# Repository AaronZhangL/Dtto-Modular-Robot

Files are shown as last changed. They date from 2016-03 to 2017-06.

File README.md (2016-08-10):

# Dtto Modular Robot
Dtto Robot v1.0 , a modular self-reconfigurable robot

A better and up to date description is available at: 
https://hackaday.io/project/9976-dtto-v10-modular-robot

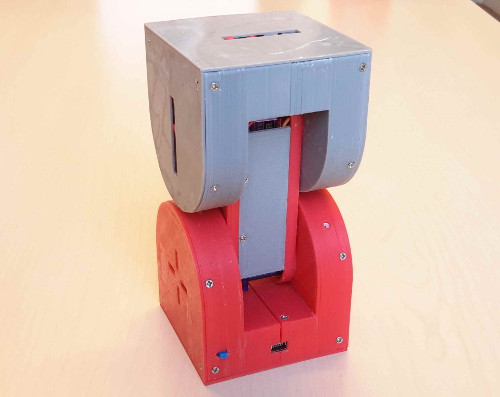
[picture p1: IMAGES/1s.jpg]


The <strong>Dtto v1.0 </strong> Robot is a modular transformable robot designed to be versatile, flexible and <strong>self-reconfigurable</strong>. The idea of modular robots is that they can adopt any shape they want, by changing the position and the connection of their modules. 

This robot is aimed for <strong>research</strong> on modular self-reconfigurable robots and educational purposes. It is designed to allow multiple modules to communicate, mechanically connect and disconnect and to work collaboratively in the locomotion, self-reconfigurability and efficient movement.

The versatility of the robot will allow it, in the future, to be able to perform <strong>rescue operations</strong>, exploration of unknown environments and <strong>space exploration</strong>.

In <strong>future</strong> works, the modules will have built in camera, ultra-sound sensor, gyroscope, accelerometer, magnetometer… The possibilities are endless.
 
This is a part of a project that is currently being developed in the <strong>Universitat Rovira i Virgili</strong>, Tarragona (Spain).

Special thanks to my project director, Dr. Jose Luís Ramírez, and to Dr. Juan González-Gómez “Obijuan”, for their support and help everytime I needed it. 

It has been fully printed with open-source 3D printers, uses open-source hardware and has been designed entirely on FreeCad.

This robot is Inspired by the MTRAN III, by The National Institute of Advanced Industrial Science and Technology (AIST), Japan. (https://unit.aist.go.jp/is/frrg/dsysd/mtran3/index.htm)

Follow the project: https://hackaday.io/project/9976-dtto-v10-modular-robot

#SPECIFICATIONS

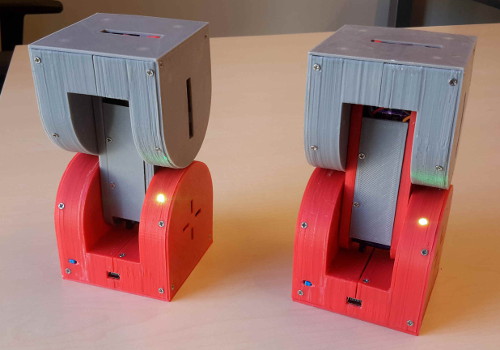
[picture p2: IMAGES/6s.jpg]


- Dimensions: 64* x 64 x 130 mm
- Weight: 210gr approx
- 2 servos TowerPro SG92R main movement (2.5kg/cm)
- 3 servos TowerPro SG90 coupling mechanism (1.8kg/cm)
- 24 Alignment magnets (4x3 neodymium disc)
- 1 Arduino nano v3.0
- 1 Bluetooth HC-06
- 1 RF. NRF2401+
- 1 WS2812 LED RGB

#VIDEOS

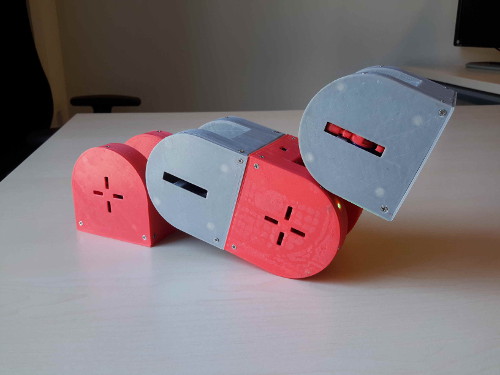
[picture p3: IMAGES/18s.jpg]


Three modules rolling
https://www.youtube.com/watch?v=pWOIe7kMd5U

One module moving, connection mechanism:
https://www.youtube.com/watch?v=O0k1wR8lxH4

Two modules connecting, moving and disconecting:
https://www.youtube.com/watch?v=2cLM48vNh7w

#CONFIGURATIONS

This is a small model showing some of the different configurations of the robot.

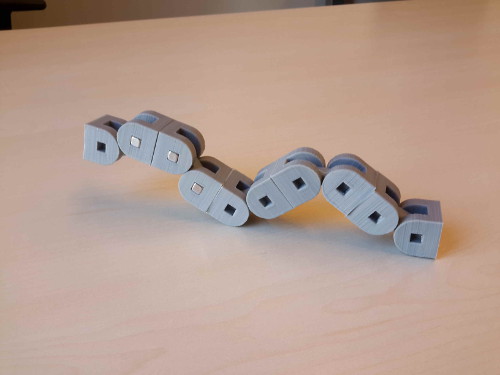
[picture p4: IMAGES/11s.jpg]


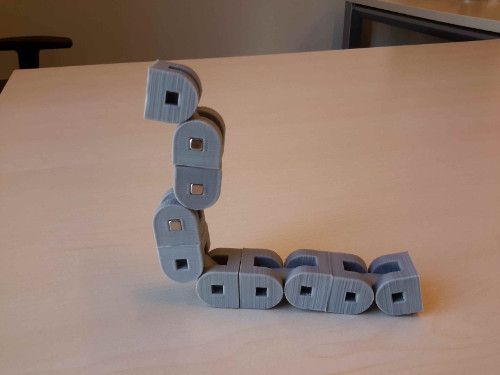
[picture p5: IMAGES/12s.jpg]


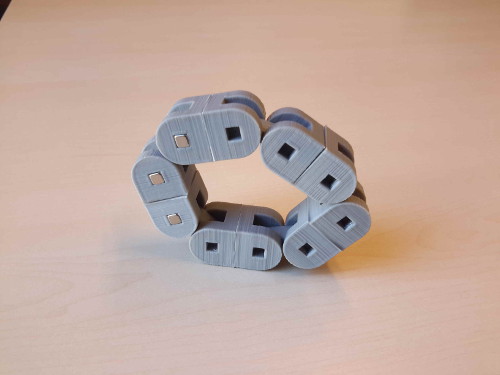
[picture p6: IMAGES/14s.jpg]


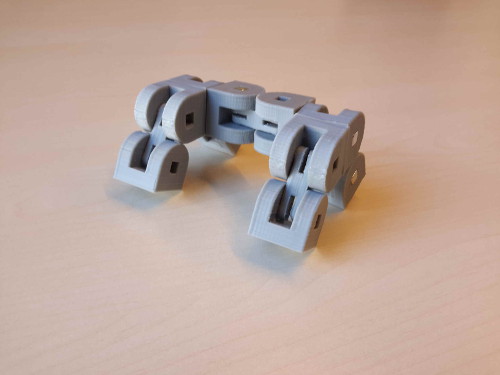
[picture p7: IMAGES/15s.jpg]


#LICENSE

This project and all of it's files, images and texts are entirely licensed under the CC BY-SA 4.0 license. (http://creativecommons.org/licenses/by-sa/4.0/legalcode)

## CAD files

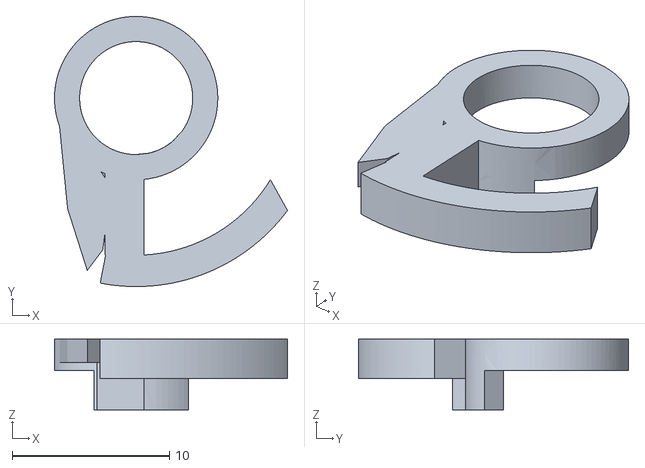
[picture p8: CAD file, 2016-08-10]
3D-printing/Dtto-v2.0.1/014-1(ganchoB001).stl
14.8 x 17.2 x 4.50

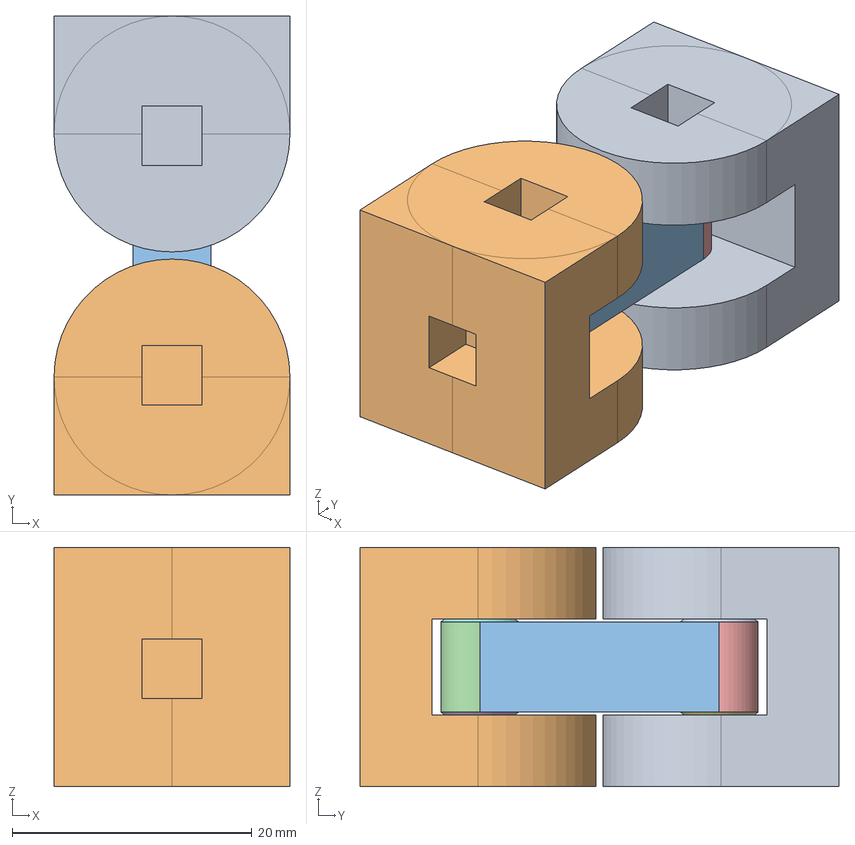
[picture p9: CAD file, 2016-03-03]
3D-printing/Freecad-files/Modelo.Escala.Dtto.v1.1.FCStd
19.7 x 40.0 x 20.0 mm
Cubo004
Cilindro002
Clone of Cilindro002
Cono001
Clone of Cono002
Clone of Cono003
Clone of Clone of Cono003

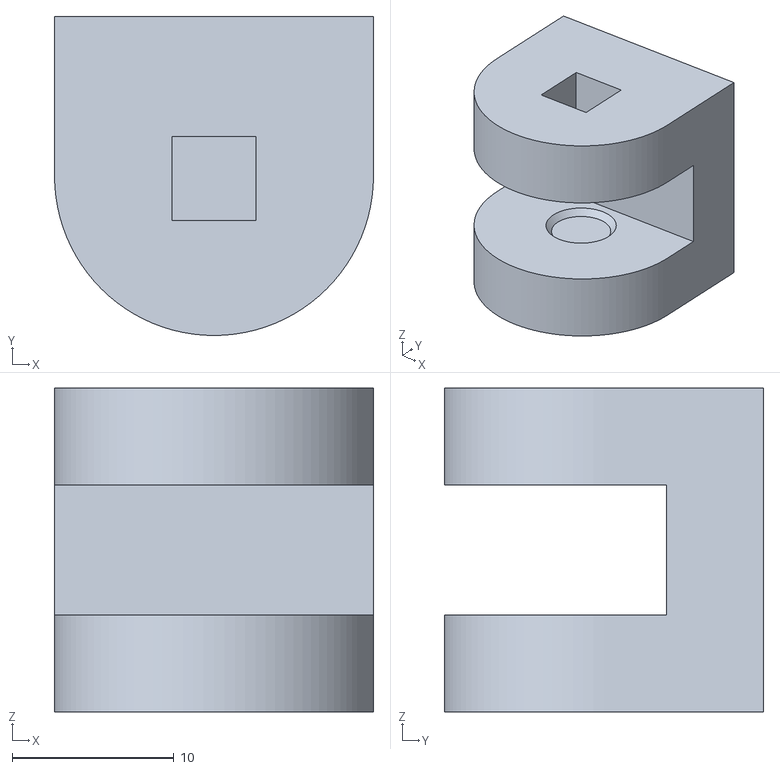
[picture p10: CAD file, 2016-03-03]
3D-printing/Small-model-v1/Male004.stl
19.7 x 19.7 x 20.0

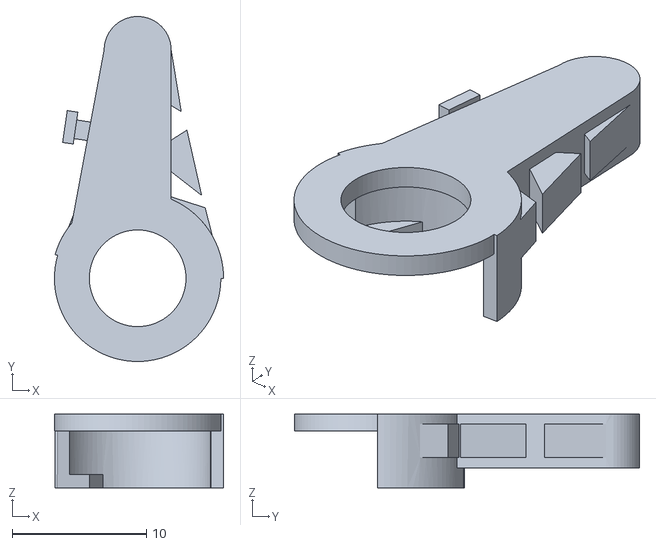
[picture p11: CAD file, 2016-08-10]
3D-printing/Dtto-v2.0.1/013-1(ganchoA002).stl
12.6 x 25.7 x 5.50

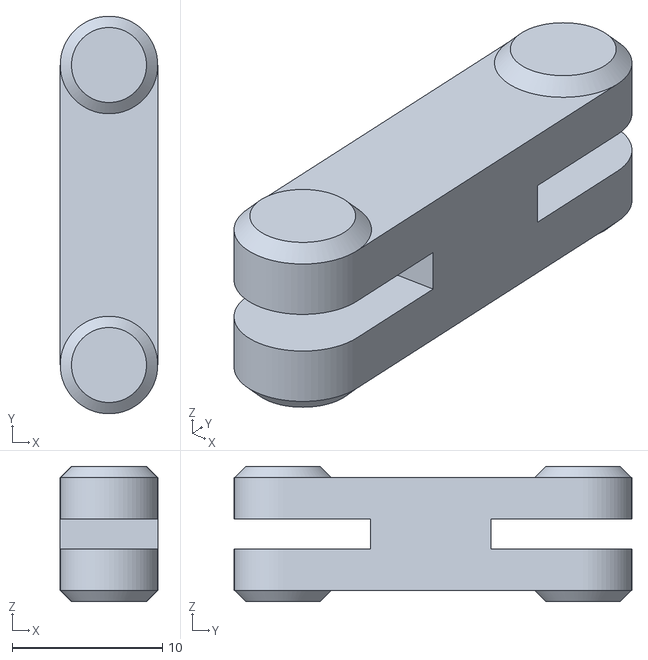
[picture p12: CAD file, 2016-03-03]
3D-printing/Small-model-v1/Brazo002.stl
6.50 x 26.5 x 9.00

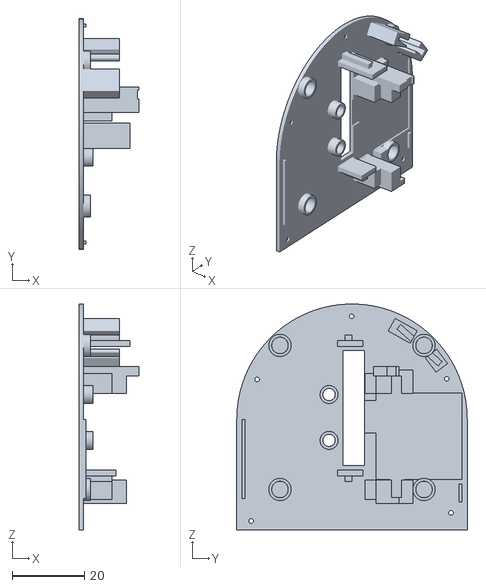
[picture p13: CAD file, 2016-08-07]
3D-printing/Dtto-v2.0.1/007-1(paredAM001).stl
16.8 x 64.0 x 62.8

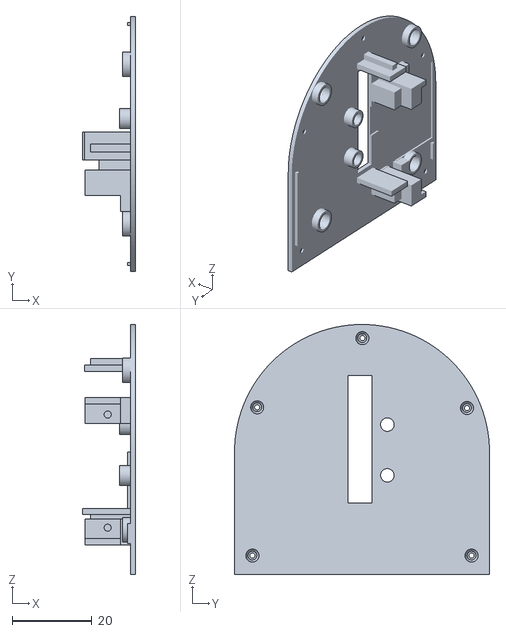
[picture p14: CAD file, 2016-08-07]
3D-printing/Dtto-v2.0.1/009-1(ParedBM001).stl
13.2 x 64.0 x 62.8

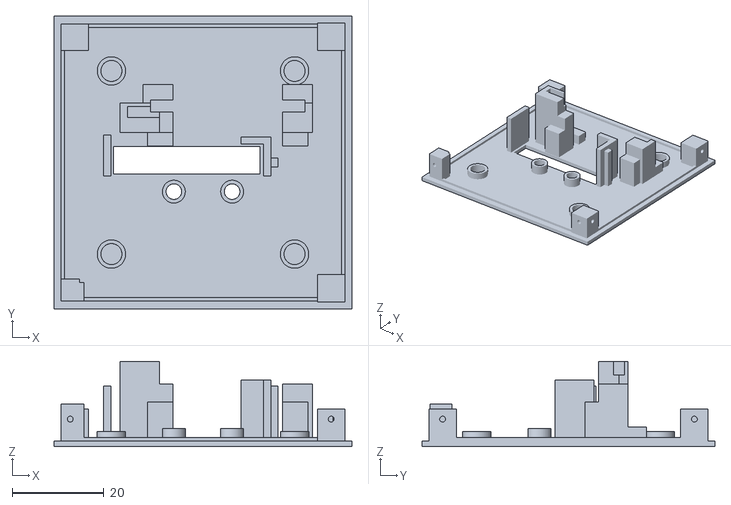
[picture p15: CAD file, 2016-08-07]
3D-printing/Dtto-v2.0.1/005-1(baseM001).stl
65.0 x 64.0 x 18.6

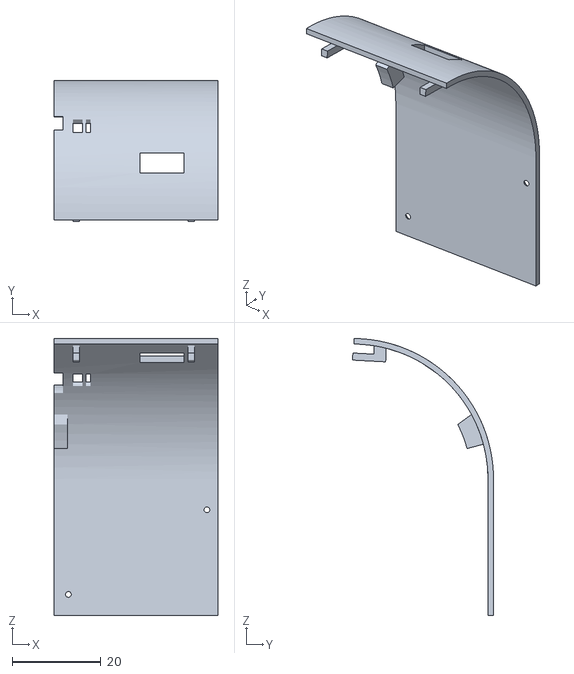
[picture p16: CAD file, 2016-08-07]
3D-printing/Dtto-v2.0.1/001-1(curvaext002).stl
37.0 x 31.8 x 62.5

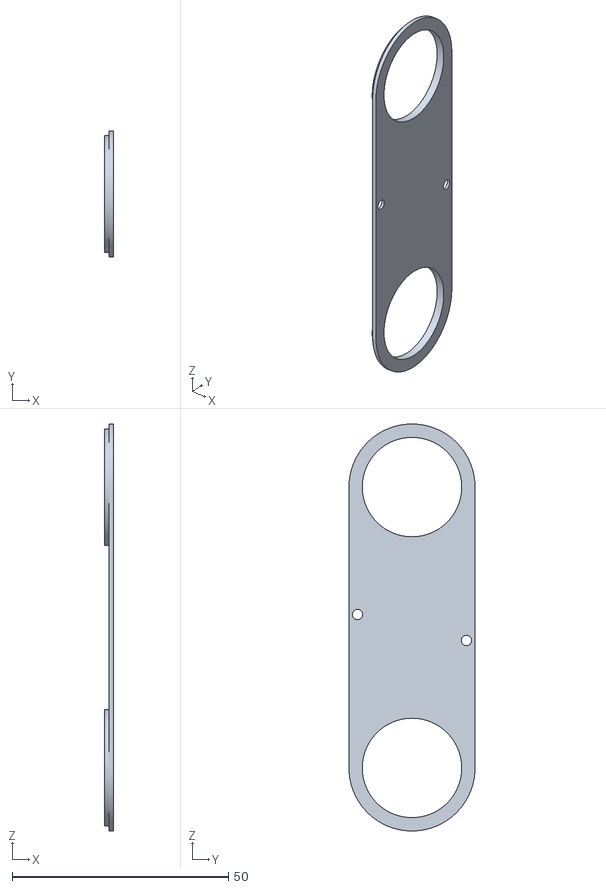
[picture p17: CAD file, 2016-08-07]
3D-printing/Dtto-v2.0.1/011-1(brazotapa002).stl
2.00 x 29.2 x 94.2

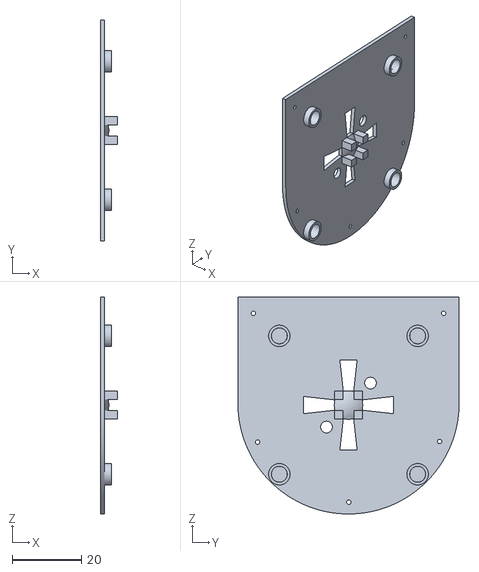
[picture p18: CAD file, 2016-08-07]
3D-printing/Dtto-v2.0.1/008-1(paredAF001).stl
5.00 x 64.0 x 62.8

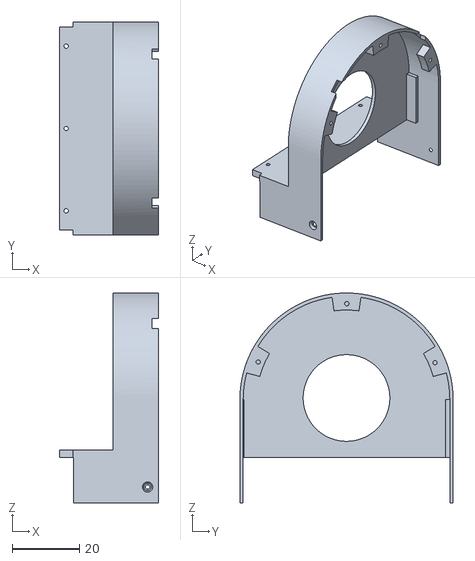
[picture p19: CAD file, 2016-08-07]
3D-printing/Dtto-v2.0.1/003-1(paredcurva003).stl
29.5 x 63.5 x 62.5

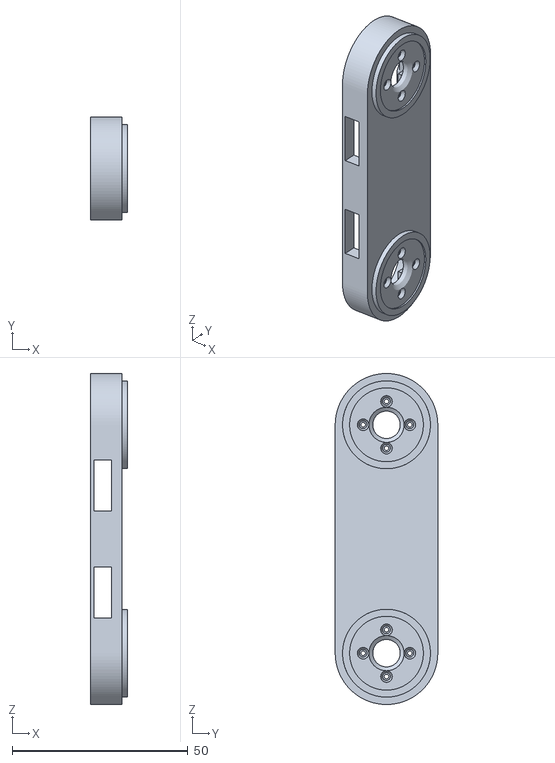
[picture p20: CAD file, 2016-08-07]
3D-printing/Dtto-v2.0.1/012-1(brazobase002).stl
10.5 x 29.2 x 94.2

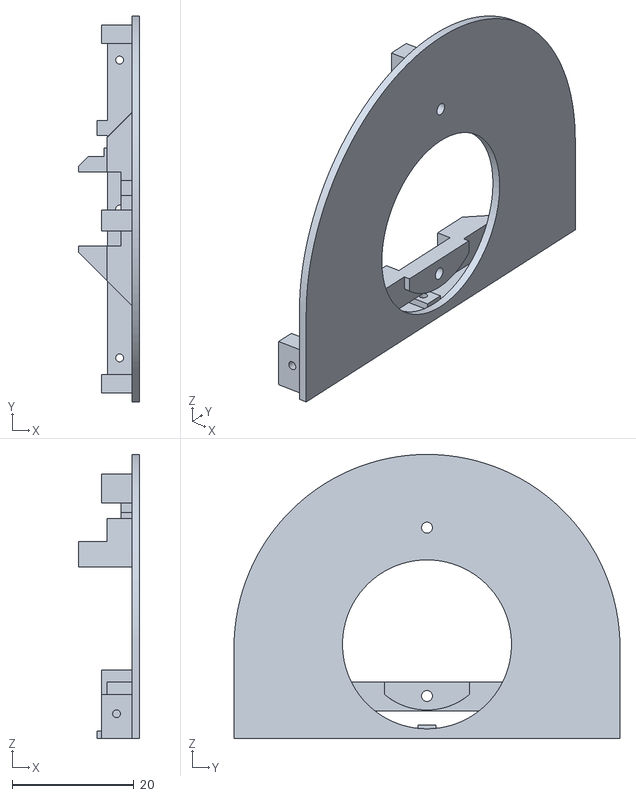
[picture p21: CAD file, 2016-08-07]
3D-printing/Dtto-v2.0.1/004-1(interior001).stl
10.0 x 63.5 x 46.8

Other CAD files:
3D-printing/Dtto-v2.0.1/002-1(curvafija002).stl
3D-printing/Dtto-v2.0.1/010-1(paredBF001).stl
3D-printing/Dtto-v2.0.1/006-1(baseF001).stl
3D-printing/Dtto-v1/ParedAM003.stl
3D-printing/Dtto-v1/CurvaAF003.stl
3D-printing/Dtto-v1/CurvaAM002.stl
3D-printing/Dtto-v1/CurvaBF003.stl
3D-printing/Dtto-v1/CurvaBM002.stl
3D-printing/Dtto-v1/ParedAF001.stl
3D-printing/Dtto-v1/ParedBF001.stl
3D-printing/Dtto-v1/ParedBM003.stl
3D-printing/Dtto-v1/baseF004.stl
3D-printing/Dtto-v1/baseM004.stl
3D-printing/Dtto-v1/brazoA001.stl
3D-printing/Dtto-v1/brazoA002.stl
3D-printing/Dtto-v1/brazoB002.stl
3D-printing/Dtto-v1/brazoBase002.stl
3D-printing/Dtto-v1/brazotapa001.stl
3D-printing/Dtto-v1/ganchoA006.stl
3D-printing/Dtto-v1/ganchoB006.stl

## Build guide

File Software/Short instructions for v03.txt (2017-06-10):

Hello!

First you should know that there is a 'master' module that you configure in the 'DttoType' definition (line 21 of 
v03 code). If you only have one module, this DttoType should be '0' (master). If you add more modules, you should 
program them with DttoType '1' (slave).

When they are connected, each module gets a number depending on the connection order (1,2,3...).

The bluetooth commands go to the rxData char array, and work like this:

- 1st character(rxData[0]): Char identifying the module you want to talk to. Ej. If you want to talk to module 1, 
this char should be '1'. If you want to talk to all the modules at the same time, you have to use athe char 'a' (all).

- 2nd character (rxData[1]):  This char is the action that the modules, or all modules, have to do. In the main 
loop 'void loop()' you have a switch case that, depending on the char on rxData[1], calls a function on the code. 
For example, if you want to call the test function, this char should be 't'.
    Command list 'rxData[1]' :
      - 's' start. moves all servomotors to the central position
      - 'r' run. starts snake movenent; 'rxData[2]' must indicate direction('m' or 'f')
      - 'e' escape. stops all other functions.
      - 'g' gancho (hook). Moves the hooks of the mechanical connection; 
        -'rxData[2]' must indicate which hook to move ('b' base, 'r' right face, 'l' left face)
        -'rxData[3]' must indicate which position to move the hook to ('0' center(hide), '1' and '2' couple or decouple)
      - 't' test. test the RGB LED on the modules
      - 'a' amplitude (experimental). change amplitude of the sinusoidal movement
      - 'f' fase (phase). change phase between motors of the sinusoidal movement

- 3rd, 4th,5... char: These characters are used as parameters in some functions, so you have to check in every 
function what does exactly do.

Examples of instructions:
  - 'arm' (All-Run-Male) starts snake movement in the male direction
  - 'at' (All-Test) blinks the RGB LED
  - '2gb0' (2ndmodule-Gancho(hook)-Base-0)moves the hook of the 2nd module to the central position
  - 'ae' (All-Escape) stops all functions, motors, LEDs of all motors.

Sorry for the bad commented code, I still have to fix it a LOT...

Alberto (10-06-2017)

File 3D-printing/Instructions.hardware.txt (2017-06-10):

*****by otrebla 333 - 03/03/2016 *****

These files have been designed to print with my personal printer,a Prusa i3
with a 0.4 nozzle and using ABS. I've printed all of them at a .25 mm layer
height.

The assembly of the parts is very simple, but the tricky part is how to manage
all the cables throught the arm. 

I will be creating the instrucions in this file as you ask.

The actual model is the 2.0.1 There will be updates soon.

There is a small model to print and simulate the big robot! 

Thanks!

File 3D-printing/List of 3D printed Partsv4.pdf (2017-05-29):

### Dtto Modular Robot - 3D Printed Parts Needed (v2.0.1)

Here there is a listing of all the 3D parts needed for building a module. They are positioned the way we think it will be best for FDM printing.

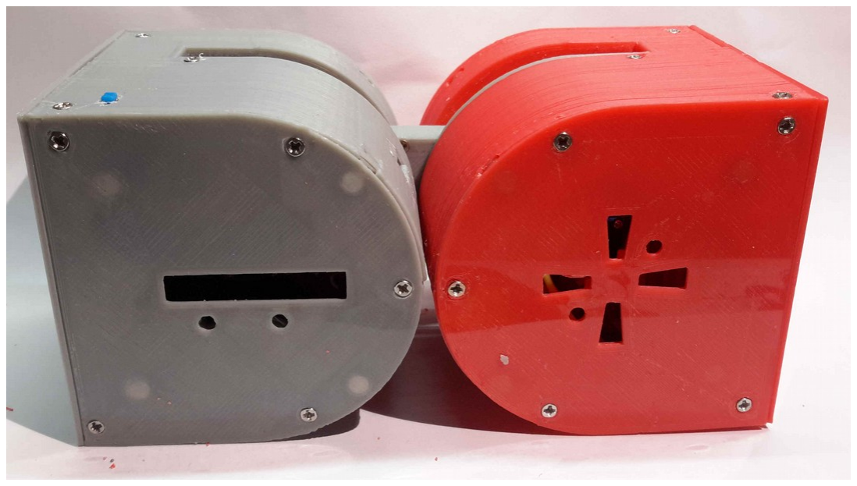
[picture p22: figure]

The module on the above picture was printed in two colours: A: Grey; B: Red.

The parts files are available for download at: https://github.com/otrebla333/Dtto-Modular-Robot Project:
https://hackaday.io/project/9976-dtto-v20-modular-robot

The parts were usually printed at 0.2mm layer height, 0.4mm nozzle size. Some parts require sanding in order to fit/slide properly.

QTY = Quantity
Part Nº | QTY | Color | Part Name | Position
001-1 | 2 | A & B | curvaext002.stl (support everywhere)

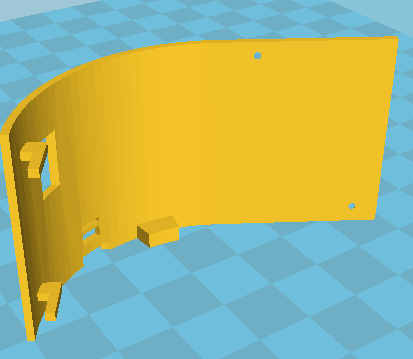
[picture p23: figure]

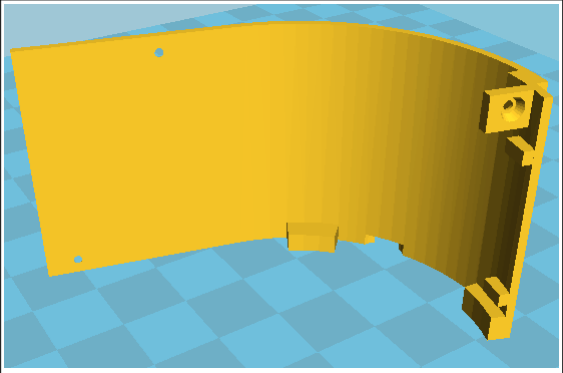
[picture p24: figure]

002-1 | 2 | A & B | curvafija002.stl (support everywhere)

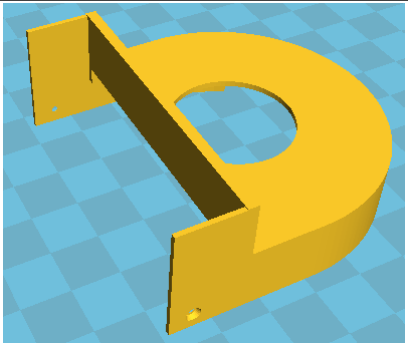
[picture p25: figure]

003-1 | 2 | A & B | paredcurva003. stl (support touching buildplate)

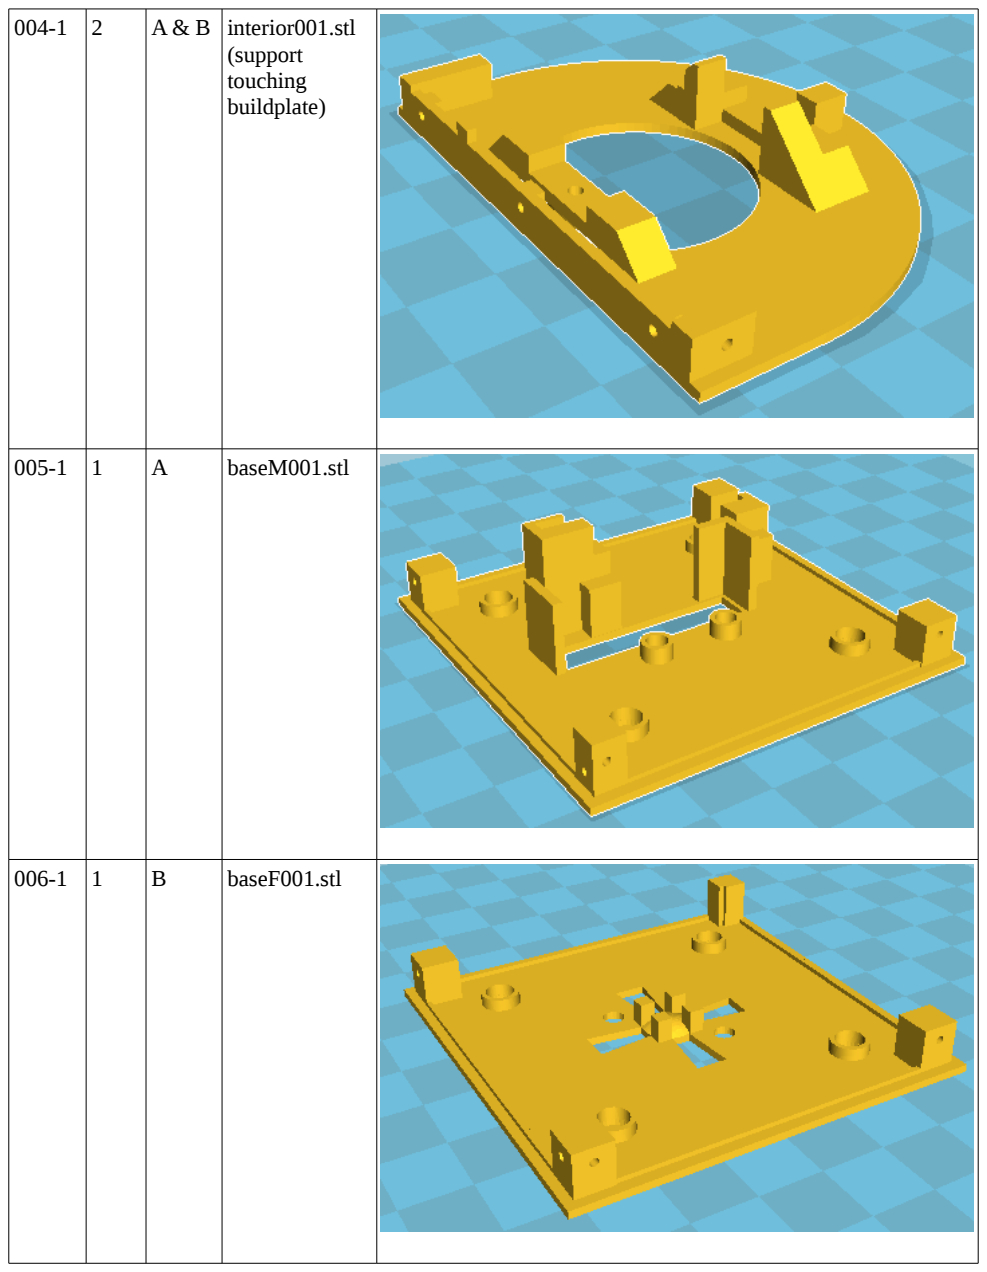
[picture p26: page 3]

004-1 | 2 | A & B | interior001.stl (support touching buildplate)
005-1 | 1 | A | baseM001.stl
006-1 | 1 | B | baseF001.stl

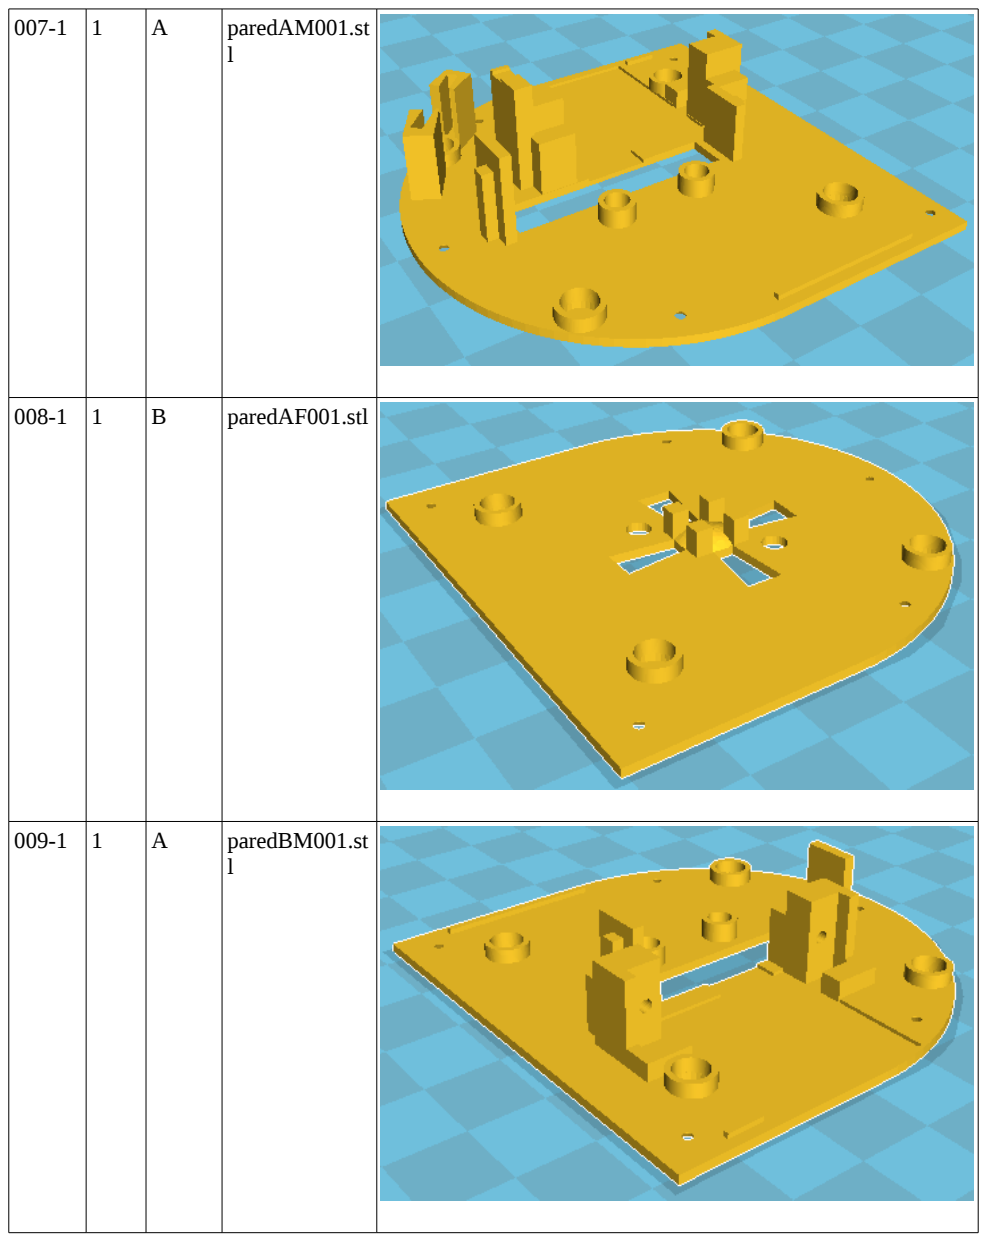
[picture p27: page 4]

007-1 | 1 | A | paredAM001.st l
008-1 | 1 | B | paredAF001.stl
009-1 | 1 | A | paredBM001.st l

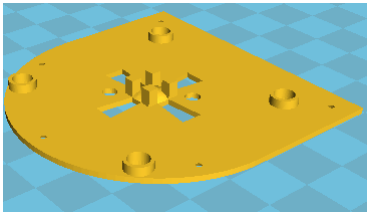
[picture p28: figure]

010-1 | 1 | B | paredBF001.stl

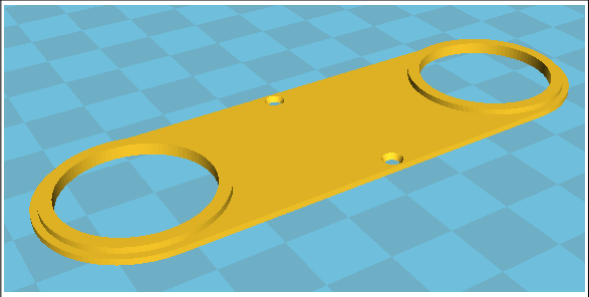
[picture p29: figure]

011-1 | 1 | A or B | brazotapa002.st l

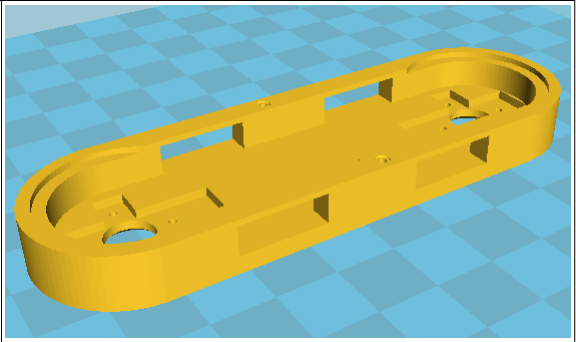
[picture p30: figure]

012-1 | 1 | A or B | brazobase002.s tl (support everywhere)

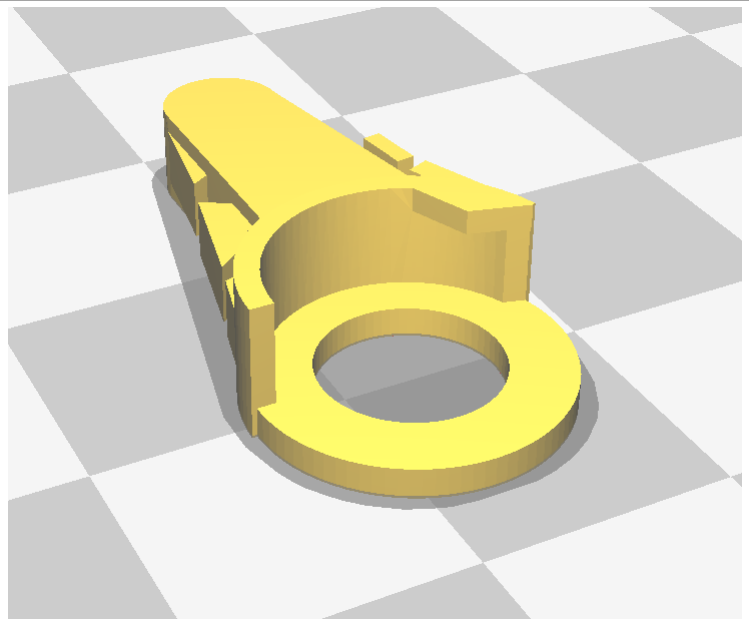
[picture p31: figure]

013-1 | 3 | A or B | ganchoA002.stl

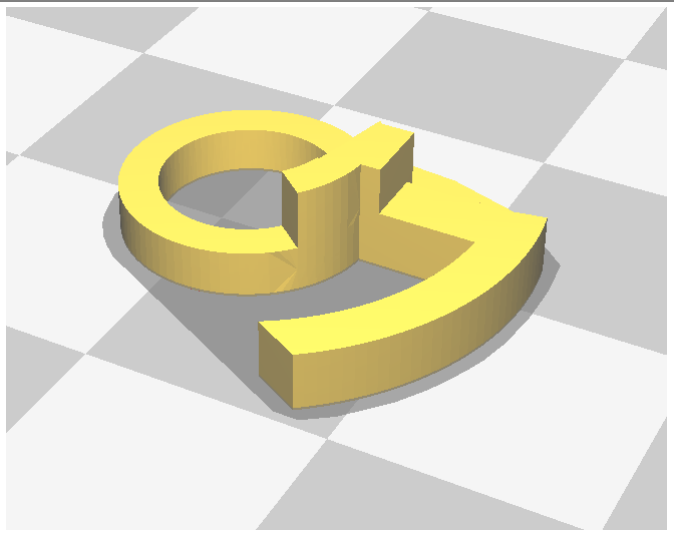
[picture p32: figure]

014-1 | 3 | A or B | ganchoB001.stl

This project and all of it's files, images and texts are entirely licensed under the CC BY-SA 4.0 license. (http://creativecommons.org/licenses/by-sa/4.0/legalcode)

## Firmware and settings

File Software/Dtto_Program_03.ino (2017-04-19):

/*
 * Código módulos Dtto:  robot modular transformable
 * Alberto Molina Pérez 
 * */


/////LIBRERIAS/////

#include <Adafruit_NeoPixel.h>
#ifdef __AVR__
#include <avr/power.h>
#endif
#include <SoftwareSerial.h>
#include <Servo.h> 
#include <SPI.h>
#include <nRF24L01.h>
#include <RF24.h>

/////DEFINITIONS///// 

#define DttoType 0//0 for MASTER module; 1 for the rest of SLAVE modules
#define METALGEAR 1 //0 for NO, 1 for YES (If you are using the MG92B,use 1. If using SG92R, use 0.

#define PIN 19 //Pin Neopixel

#define CE_PIN 2  //RF pin
#define CSN_PIN 4  //RF pin

int SCenterM =83;     //Center position of Male and Female main motors
int SCenterF =83;
#define SCenterB 83   //Center, min and max position of coupling mechanism
#define SMinB 5
#define SMaxB 150

/////CONTROL SINUSOIDAL (snake movement) /////


#define vel 0.002 //Speed (w)
//
int ampl = 40; //Amplitude
float desfase = 3.14; // Phase between modules(motores*2)
float desfaseint = 3.14;
unsigned long t = 0;    //Time auxiliar variables
unsigned long t2 = 0;
unsigned long t_start=0;
byte reset=1;



/////INICIALIZACIONES/////

Adafruit_NeoPixel strip = Adafruit_NeoPixel(1, PIN, NEO_GRB + NEO_KHZ800);  //number of pix, arduino PIN, pixel type flags

SoftwareSerial bluetooth(7,8); //Creating software serial for bluetooth module (RX,TX)

//NRF module configuration
const uint64_t pipes[2] = {0xE8E8F0F0E1LL,0xF0F0F0F0D2LL}; // Define the transmit pipe rf
char RFData[6];
char addmodRF[2]={'a','+'};
RF24 radio(CE_PIN, CSN_PIN); // Create a Radio

/////VARIABLES PROGRAMA/////

//bt
char rxChar;    // Serial port receiving variable
int ledpin = 13;  // Pin donde se encuentra conectado el led (pin 13)

String rxDataBT; //Datos recibidos por BT - BT received data
char rxDataBT2[6]; //Datos recibidos por BT convertidos a char array - BT data converted to char array
char rxDataRF[6]; //Data recibida por RF, valorar si es para ese modulo - NRF received data
char rxData[6]; //Data internal para el modulo - Clean received data
char rxServo;
int angle;
int w0;
int w1;
int w2;
int i=0;
int j=0;

int modnum=1;
int modtotal=1;

//SERVO definitions (Calibrate according to real module for accuracy)
Servo servoM;
int posM = 82;//MIN 001, MAX 172
Servo servoF;
int posF = 83;//MIN002, MAX 174
Servo servoB;
int posB = 82;
Servo servoR;
int posR= 80;
Servo servoL;
int posL = 80;

///// Rotating movement variables

#define vel2 0.001 //Speed (w)
byte stepc = 0;
byte inicio=0;
byte next = 0;

  unsigned long started_at = millis();
  bool timeout2 = true; 
  int sync_ok=0;
  int sync_data[2];

  
void setup() 
{

    if (METALGEAR) //Correcting for MG92B motors
    {
      SCenterM =90;
      SCenterF =90;
    }
  // put your setup code here, to run once:
    Serial.begin(9600);
    delay(3000);
    
    radio.begin();  //Starts NRF (radio)
    //radio.setRetries(15,5); //Intentos de reenvio en caso de mala comunicacion
    
    if (DttoType==0)      //If module is a master: Start bluetooth and writing channel NRF radio
    {
      bluetooth.begin(9600);
      bluetooth.println("Reset");
      radio.openWritingPipe(pipes[0]);
      radio.openReadingPipe(1,pipes[1]);
      //radio.openWritingPipie(pipes[2]);
      radio.startListening();
    }
    else                  //IF module is a slave: Start reading channel NRF radio
    {
      radio.openWritingPipe(pipes[1]);
      radio.openReadingPipe(1,pipes[0]);
      //radio.openReadingPipe(2,pipes[2]);  
    }
  
    if (DttoType==1) getmodulenum(); //If slave, ask master module for a number
    //Start Neopixel LED
    strip.begin();
    strip.setBrightness(255);
    strip.setPixelColor(0,0,100,0);
    strip.show();
        
        
       


}


void loop() 
{  
   
  if(DttoType==0)
  {
    assignmodulenum();
    listenBluetooth();
  }
  else 
  {
    listenRF();
  }
      //rxData[1]='r';
      //rxData[2]='m';
      switch (rxData[1])
                
                 {
                    case 's': //start, initial position
                        start();
                      break;
                    case 'r': //Run, sinusoidal control
                        snake();
                      break;
                    case 'e'://Escape
                        escape();
                      break;
                    case 'm'://manual movement
                        manual();
                      break;
                    case 'g'://attach module
                        gancho();
                      break;
                    case 't'://test communications
                        test_comm();
                      break;
                    case 'a'://modificar Amplitud
                        amplitud();
                      break;
                    case 'f'://modificar Fase
                        fase();
                      break;
                    case '+':
                        modtotal++;
                        rxData[1]='e';
                        Serial.println(modtotal);
                        break;
                    case 'h'://test communications
                        modtotal=1;
                        rxData[1]='e';
                      //break;
                    default:
                      break;
                  }
  }


void amplitud()
{
      w0=(rxData[2]-'0')*100;
      w1=(rxData[3]-'0')*10;
      w2=rxData[4]-'0';
      ampl=w0+w1+w2;
      rxData[1]='e';
}

void fase()
{
      w0=(rxData[2]-'0')*100;
      w1=(rxData[3]-'0')*10;
      w2=rxData[4]-'0';
      desfaseint=w0+w1+w2;
      desfaseint=(desfaseint*3.1415)/180;
      desfase=desfaseint;
      rxData[1]='e';
}

void getmodulenum()
{
  int peticion=1234;
  detachServos();
  while (modnum==1)
  { 
      radio.stopListening();
      radio.write(&peticion,sizeof(int));
      radio.startListening();
      unsigned long started_waiting_at = millis();
      bool timeout = false;
      while ( ! radio.available() && ! timeout )       // Esperamos 200ms
      {
          if (millis() - started_waiting_at > 500 )timeout = true;
      }
      if ( ! timeout )
      {   // Leemos el mensaje recibido
           int got_num;
           radio.read(&got_num, sizeof(int) );
           modnum=got_num;
           modtotal=modnum-1;
      }
  }
}


void assignmodulenum()
{
  
      //detachServos();
      if ( radio.available())
      {   // Leemos el mensaje recibido
           int got_peticion;
           int addmod;
           radio.read(&got_peticion, sizeof(int) );
           if (got_peticion==1234)
            {
              radio.stopListening();
              modtotal++;
              radio.write(&modtotal,sizeof(int));              
              radio.write(&addmodRF,6); 
              radio.startListening();
              
            }
      }
}

void listenBluetooth()
{
  
  if( bluetooth.available()>1 ) //Aqui hay num de bytes disponibles up to 64 bytes
  {  
    //  Detach servos para que no crear interferencias con softwareSerial.
      //radio.stopListening();
      detachServos();
      rxDataBT= bluetooth.readStringUntil('\0'); 
      //radio.startListening();
      rxDataBT.toCharArray( rxDataBT2,6 );      
       //Check DATA syntax?? 
      if(rxDataBT2[0]=='1')
        {
            for(i=0;i<6;i++)
            {
              rxData[i]=rxDataBT2[i];
            }
                
        }
      else if (rxDataBT2[0]=='a')
        {
            for(i=0;i<6;i++)
            {
              RFData[i]=rxDataBT2[i];
              rxData[i]=rxDataBT2[i];
            }
            radio.stopListening();
            radio.write( RFData, 6 );
            radio.startListening();
        }
      else
        {
          for(i=0;i<6;i++)
            {
              RFData[i]=rxDataBT2[i];
            }
            radio.stopListening();
            radio.write( RFData, 6 );
            radio.startListening();
        }
  }
  //
}


void syncMaster()
{
            sync_data[0]='S';
            delay(1);
            radio.stopListening();
            radio.write( &sync_data, sizeof(int) );
            radio.startListening();

}

void listenRF()
{
  if ( radio.available() )
  {
    // Read the data payload until we've received everything
   detachServos();
   while (radio.available())
   {
      // Fetch the data payload
      radio.read( rxDataRF, 6 );
    }
      
   if((rxDataRF[0]== (modnum+48))||(rxDataRF[0]=='a') )
   {
    for(i=0;i<6;i++)
            {
              rxData[i]=rxDataRF[i];
            }
   }
   //attachServos();  
  }
}

void gancho()
{
  int rxData2OLD;
  int rxData3OLD;
  
  if ((rxData[2]!=rxData2OLD)||(rxData[3]!=rxData3OLD))
  {  
    switch(rxData[2])
    {
      case 'b':
        servoB.attach(10);
        if (rxData[3]=='0')posB=SCenterB;
        else if (rxData[3]=='1')posB=SMinB;
        else if (rxData[3]=='2')posB=SMaxB;
        servoB.write(posB);      
        break;
      case 'r': 
        servoR.attach(3); 
        if (rxData[3]=='0')posR=SCenterB;
        else if (rxData[3]=='1')posR=SMinB;
        else if (rxData[3]=='2')posR=SMaxB;
        servoR.write(posR);      
        break;
      case 'l':  
        servoL.attach(9);
        if (rxData[3]=='0')posL=SCenterB;
        else if (rxData[3]=='1')posL=SMinB;
        else if (rxData[3]=='2')posL=SMaxB;
        servoL.write(posL);      
        break;
      default:
        break;
    }
    rxData2OLD=rxData[2];
    rxData3OLD=rxData[3];
    delay(150);
    
  }
  detachServos();
}

void start()

{
  attachServos();
  posM = SCenterM;
  posF = SCenterF;
  posB = SCenterB;
  posR = SCenterB;
  posL = SCenterB;
  writeServos();
  delay(250);
  detachServos();

}

void snake()
{ 
  attachServos();
  if(reset) t_start=millis();
  t=millis()- t_start;
  reset=0;
  //Serial.println(posM);
  //Serial.println(posF);
  switch(rxData[2])
  {
    case 'm':
      posM=SCenterM+ampl*sin((vel*t)+(modnum*desfase));   
      posF=SCenterF+ampl*sin((vel*t)+((modnum*desfase)+((desfase)/2))); 
      servoM.write(posM);
      servoF.write(posF);      
      break;
    case 'f':
      posM=SCenterM+ampl*sin((vel*t)-(modnum*desfase));   
      posF=SCenterF+ampl*sin((vel*t)-((modnum*desfase)+((desfase)/2))); 
      servoM.write(posM);
      servoF.write(posF);
      break;
    case 'c':
        switch(modtotal)
            {
            case 3:
              if (stepc == 0) 
              {
                if (modnum==1) 
                {
                  servoB.write(5);
                  delay(1000);
                  stepc=1;
                  delay(1000);
                  servoM.write(0);
                  servoF.write(178);
                  delay(1000);
                }
                else if (modnum==2) 
                {
                  servoB.write(5);
                  delay(1000);
                  stepc=3;
                  delay(400);
                  servoM.write(0);
                  servoF.write(85);
                  delay(600);
                  delay(1000);
                }
                else if (modnum==3) 
                {
                  delay(1000);
                  stepc=2;
                  servoM.write(85);
                  servoF.write(178);
                  delay(1000);
                  delay(1000);
                  servoB.write(5);
                }
                delay(1000);
                t_start=millis();
                next=0;
                
              }
              if(next) 
              {
                stepc++;
                if (stepc ==4) stepc =1;
                delay(500);
                t_start=millis();   
                next=0;    
              }
                t=millis()- t_start;
             
              switch(stepc)
              {
                case 1:
                  posM=85*sin((vel2*t)); 
                  if (posM>83) next++;  
                  servoM.write(posM);
                  servoF.write(178);
                  break;
                case 2:
                  posM=85-85*sin((vel2*t));
                  if(posM<1)posM=0;
                  posF=178-93*sin((vel2*t));
                  if(posF<87)next++;
                  servoM.write(posM);
                  servoF.write(posF);
                  
                  break;
                case 3:
                  posF=85+93*sin((vel2*t));
                  if(posF>176)next++;
                  servoM.write(0);
                  servoF.write(posF);
                  
                  break;
                default:
                break;  
              }
              break;
            break;
            case 4:
              if (stepc == 0) 
              {
                if (modnum==1) 
                {
                stepc=1;
                servoB.write(5);
                delay(2500);
                servoF.write(178);
                servoM.write(2);
                delay(1000);
                }
                else if (modnum==2) 
                {
                  stepc=3;
                  servoB.write(5);
                  delay(3500);
                }
                else if (modnum==3) 
                {
                  stepc=1;
                  servoB.write(5);
                  delay(500);
                  servoM.writeMicroseconds(700);
                  delay(1000);
                  servoF.writeMicroseconds(2288); 
                  delay(2000);
                }
                else if (modnum==4) 
                {
                  stepc=3;
                  servoF.write(178);
                  delay(1500);
                  servoF.write(85);
                  delay(2000);
                  servoB.write(5);

                }
                delay(1000);
                t_start=millis();
                next=0;
                
              }
              if(next) 
              {
                stepc++;
                if (stepc ==5) stepc =1;
                delay(400);
                t_start=millis();   
                next=0;    
              }
                t=millis()- t_start;
             
              switch(stepc)
              {
                case 1:
                  posM=85*sin((vel2*t)); 
                  if (posM>83) next++;  
                  servoM.write(posM);
                  servoF.write(178);
                  break;
                case 2:
                  posF=178-93*sin((vel2*t));
                  if(posF<87)next++;
                  servoM.write(86);
                  servoF.write(posF);
                  
                  break;
                case 3:
                  posM=85-85*sin((vel2*t));
                  if(posM<1)next++;        
                  servoM.write(posM);
                  servoF.write(87);       
                  break;
                case 4:
                  posF=85+93*sin((vel2*t));
                  if(posF>176)next++;
                  servoM.write(1);
                  servoF.write(posF); 
                  break;
                default:
                break;  
              }
              break;
            break;
            }
    default:
      break;
  }
  //detachServos();
}

void manual()
{
    //Lectura angulo introducido
      w0=(rxData[3]-'0')*100;
      w1=(rxData[4]-'0')*10;
      w2=rxData[5]-'0';
      angle=w0+w1+w2;
      if ((angle<=180)&&(angle>=0))
      {
           switch (rxData[2])         
           {
              case 'm':
                  servoM.write(angle);
                break;
              case 'f':
                  servoF.write(angle);
                break;
              default:
        
                break;
            }
      }
}
void escape()
{
  t=0;
  detachServos();
  strip.setPixelColor(0,0,100,0);
  strip.show();
  reset=0;
  stepc=0;
  next=0;
  inicio=0;
}

void attachServos()
{
  servoM.attach(6);
  servoF.attach(5);
  servoB.attach(10);
  servoR.attach(3);
  servoL.attach(9);
}
  
void writeServos()
{
  servoM.write(posM);
  servoF.write(posF);
  servoB.write(posB);
  servoR.write(posR);
  servoL.write(posL);
}

void detachServos()
{
  servoM.detach();
  servoF.detach();
  servoB.detach();
  servoR.detach();
  servoL.detach();
}

void test_comm()
{
      
      if((millis()- started_at)>500) strip.setPixelColor(0,0,0,100);
      else strip.setPixelColor(0,100,0,0);
      if((millis()- started_at)>1000) started_at=millis();
      strip.show();
      
}
